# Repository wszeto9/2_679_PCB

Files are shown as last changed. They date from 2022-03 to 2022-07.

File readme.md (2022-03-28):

# 2.679/2.007 Carrier Board
High Power throughput board for the 2.007 "Legacy" Robotics Competiton @ MIT, Spring 2022

[Interactive BOM](https://htmlpreview.github.io/?https://raw.githubusercontent.com/wszeto9/2_679_PCB/main/bom/ibom.html)

<h2> Features:</h2>
<ul>
<li>20A socketable fused input</li>
<li>Reverse polarity protection with warning lights and buzzer to alert incorrect wiring</li>
<li>9V USB-C Power Delivery Input to run off larger battery packs during testing</li>
<li>Protection Circuit to prevent USB-C from backcharging battery</li>
<li>Motor headers with 8.2V Output</li>
<li>Adjustable Servo voltage from 5V to Battery voltage</li>
<li>6A Syncronous Buck converter to reduce the voltage difference between the servo voltage and battery boltage</li>
<li>16 Actuator Ports (8 individually controllable)</li>
<li>Comparator Circuit for light based start signal, directly wired to an Arduino Interrupt</li>
<li>Mechanically Adjustable trigger point for photoresistor interrupt input</li>
<li>8-channel RC controller input for compatability with Gobilda RC Receiver</li>
<li>MPU6050 and LSM6DS33 Header for heading measurements with interrupt pins connected to D2</li>
<li> 5V and 3.3V I2C headers for a multitude of sensor inputs</li>
<li>ARGB Debugging LEDs to offer more variations of debugging signals</li>
<li>ARGB Header to decorate robot in <i><b>light</b></i></li>
<li>Breakout boards for Hall Effect Sensors, In-Line current sensors, and I/O Breakout boards </li>
<li>Fun Silkscreen messages for my favorite professors </li>
</ul>

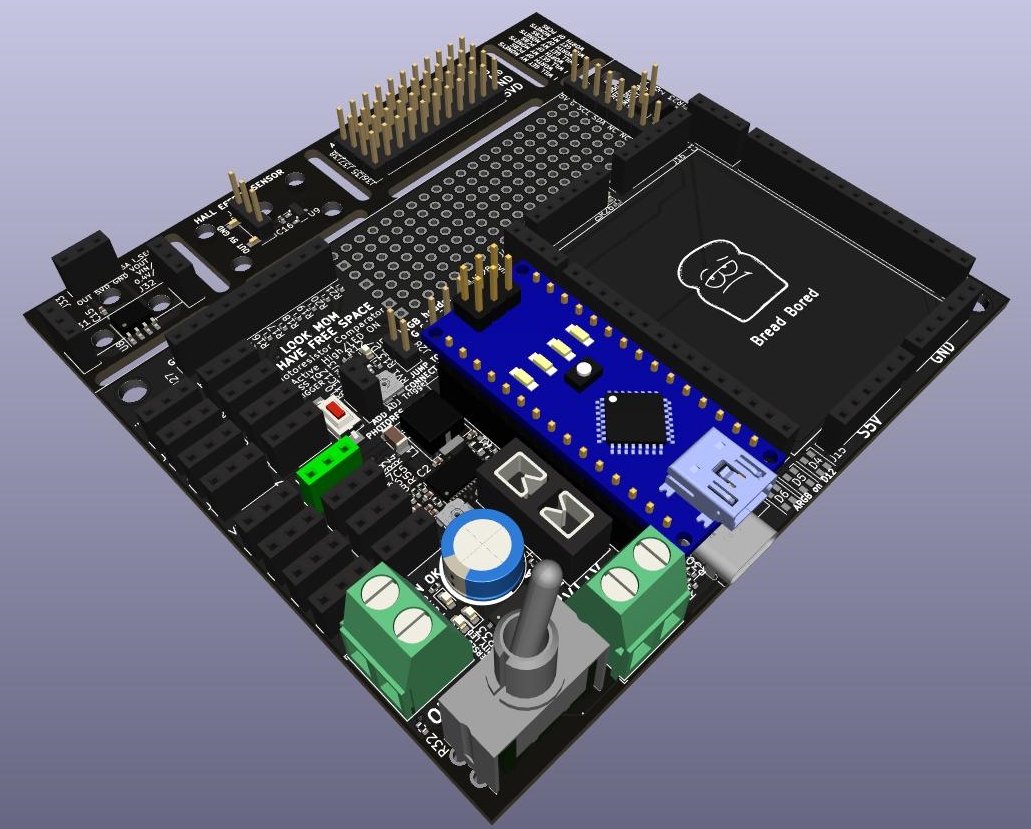
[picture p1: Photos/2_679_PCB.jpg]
3D Assembled

PCBA

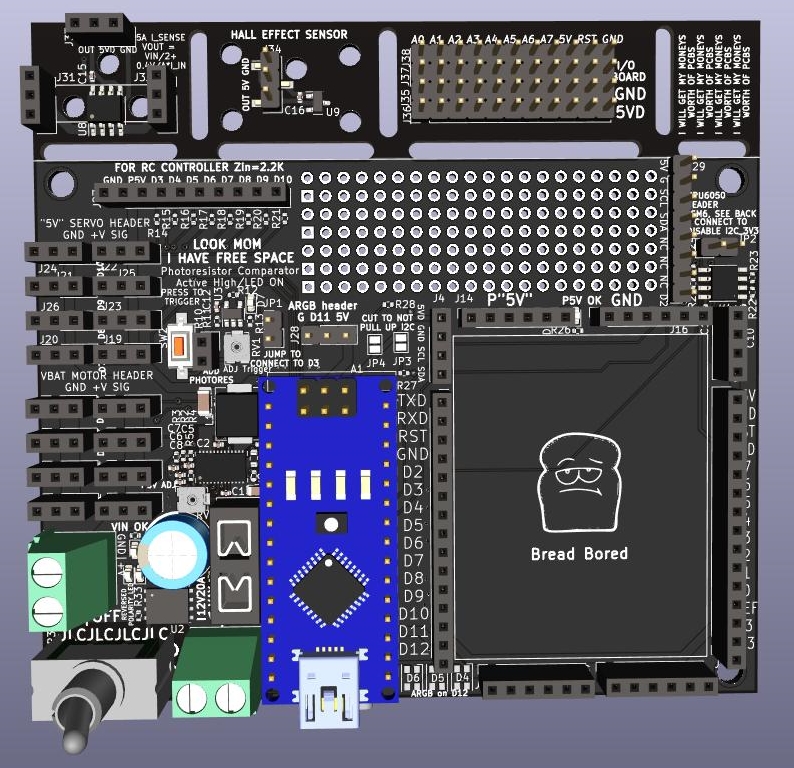
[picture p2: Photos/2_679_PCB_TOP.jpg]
Top

Top

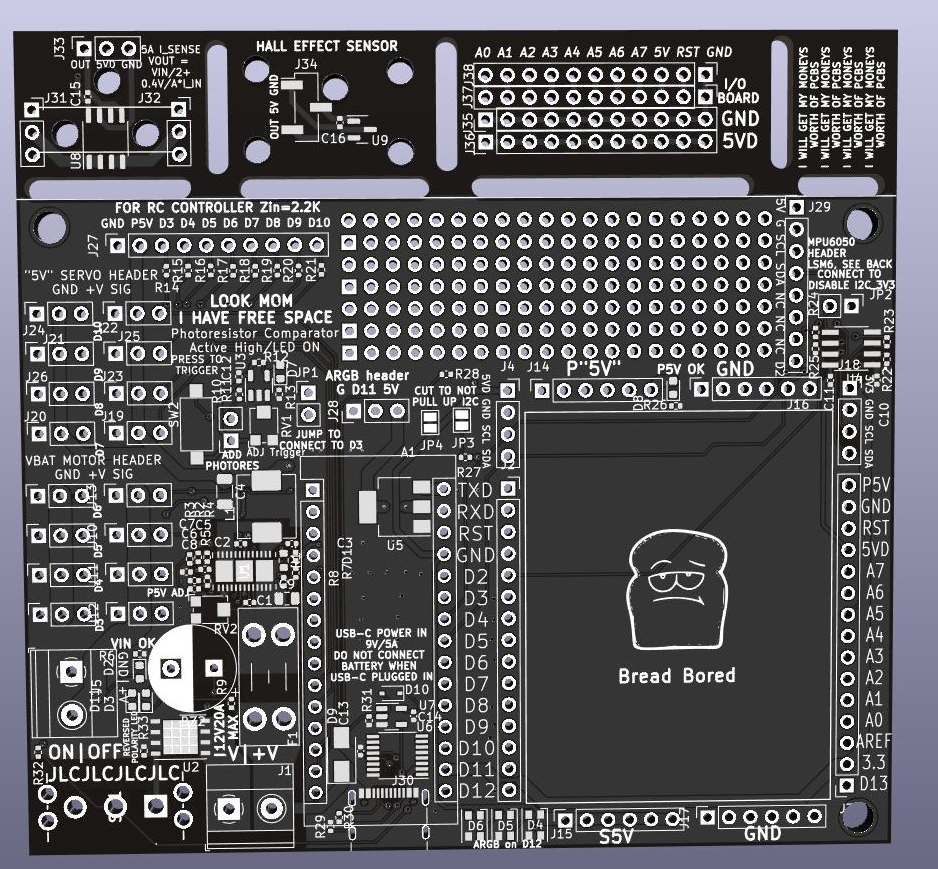
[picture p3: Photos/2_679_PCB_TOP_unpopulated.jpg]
Top_unpopulated

Top Unpopulated Board

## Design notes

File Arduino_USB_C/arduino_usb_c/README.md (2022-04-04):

# 2.007 Power Distribution Board
Battery protection circuit for 2.007 "Legacy" Robotics Competiton @ MIT, Spring 2022

[Interactive BOM](https://htmlpreview.github.io/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)

<h2> Features:</h2>
<ul>
<li>20A socketable fused input</li>
<li>Reverse polarity protection</li>
<li> Voltage Monitoring components to prevent overdischarging of batteries </li>
  <li> Black colored Arduino Nano for looks </li>
  <li> Op-Amp breakout board for additional gain on current sensors</li>
</ul>

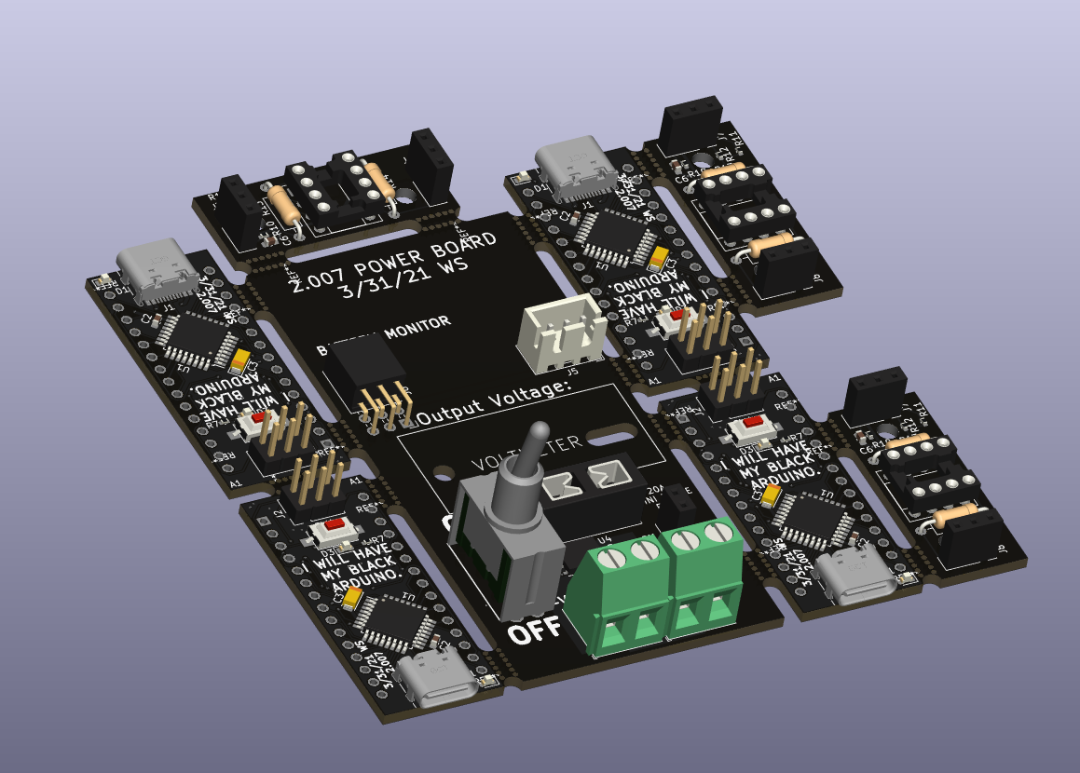
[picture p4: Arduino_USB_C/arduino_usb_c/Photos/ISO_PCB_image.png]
3D Assembled

PCBA

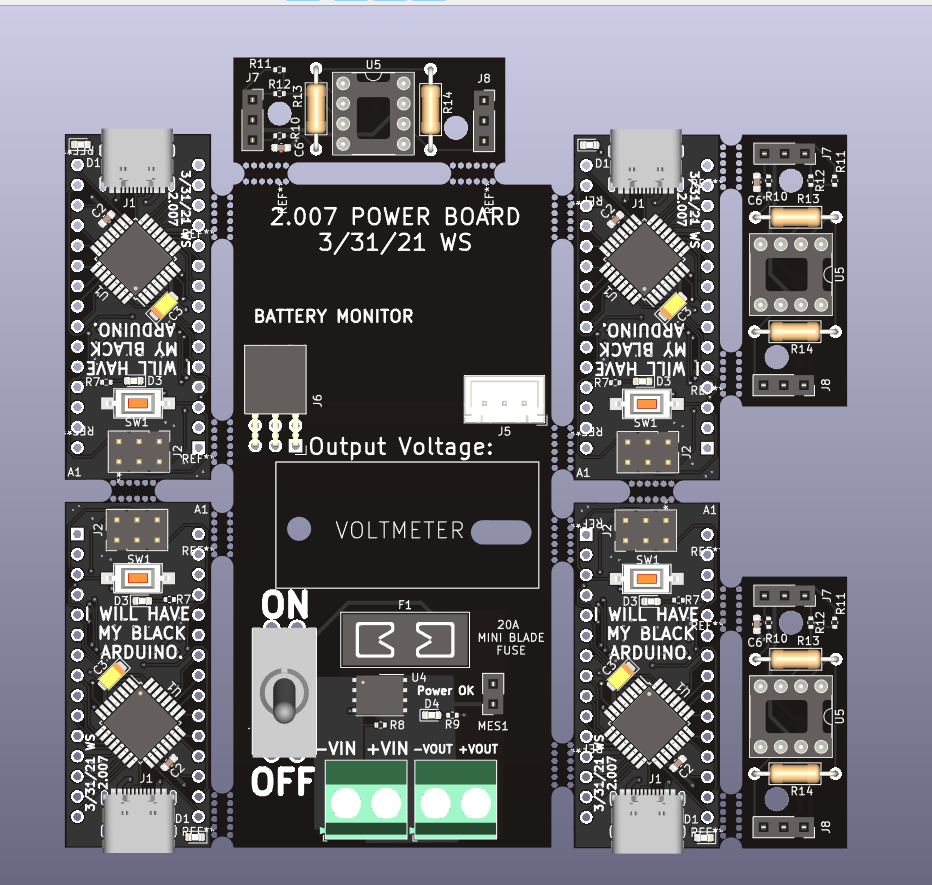
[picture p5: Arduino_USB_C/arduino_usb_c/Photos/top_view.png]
Top

Top

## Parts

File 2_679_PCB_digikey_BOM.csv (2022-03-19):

Item | Qty | Reference(s) | Value | LibPart | Footprint | Datasheet | Digikey
1 | 1 | A1 | Arduino_Nano_v3.x | MCU_Module:Arduino_Nano_v3.x | Module:Arduino_Nano | http://www.mouser.com/pdfdocs/Gravitech_Arduino_Nano3_0.pdf | 1738-1026-ND
2 | 1 | BZ2 | Buzzer | Device:Buzzer | Capacitor_THT:CP_Radial_D10.0mm_P5.00mm | https://www.digikey.com/en/products/detail/pui-audio-inc/AI-1027-TWT-5V-2-R/5011389 | 668-1454-ND
11 | 1 | D1 | D_Schottky | Device:D_Schottky | Diode_SMD:D_0402_1005Metric | https://www.digikey.com/en/products/detail/comchip-technology/CDBQR0130R/1973506 | 641-1272-1-ND
13 | 3 | D4, D5, D6 | 3528 ARGB LED | :SK6812MINI_1 | LED_SMD:LED_Cree-PLCC4_3.2x2.8mm_CCW | https://www.digikey.com/en/products/detail/american-bright-optoelectronics-corporation/BB-HRGB32M-TRB-C/13179345 | 2007-BB-HRGB32M-TRB-CCT-ND
16 | 1 | F1 | 20A | Device:Fuse_Small | Fuse:Fuseholder_Blade_Mini_Keystone_3568 | https://www.digikey.com/en/products/detail/keystone-electronics/3568/2137306 | 36-3568-ND
17 | 2 | J1, J5 | POWER_IN | Connector:Screw_Terminal_01x02 | TerminalBlock_Phoenix:TerminalBlock_Phoenix_MKDS-1,5-2_1x02_P5.00mm_Horizontal | https://www.digikey.com/en/products/detail/te-connectivity-amp-connectors/796949-2/2223908 | 796949-2-ND
18 | 2 | J2,J3 | ARDUINO_HEADER_1 | Connector:Conn_01x15_Female | Connector_PinSocket_2.54mm:PinSocket_1x15_P2.54mm_Vertical | https://www.digikey.com/en/products/detail/sullins-connector-solutions/PPTC151LFBN-RC/810153 | S7013-ND
20 | 2 | J4, J18 | I2C_5V | Connector:Conn_01x04_Female | Connector_PinSocket_2.54mm:PinSocket_1x04_P2.54mm_Vertical | https://www.digikey.com/en/products/detail/sullins-connector-solutions/PPTC041LFBN-RC/810144 | S7002-ND
22 | 20 | J6, J7, J8, J9, J10, J11, J12, J13, J19, J20, J21, J22, J23, J24, J25, J26, J31, J32, J33, J28 | DC Motor Header | Connector:Conn_01x03_Female | Connector_PinSocket_2.54mm:PinSocket_1x03_P2.54mm_Vertical | https://www.digikey.com/en/products/detail/sullins-connector-solutions/PPPC031LFBN-RC/810175 | S7036-ND
23 | 4 | J14, J15, J16, J17 | Conn_01x06_Female | Connector:Conn_01x06_Female | Connector_PinSocket_2.54mm:PinSocket_1x06_P2.54mm_Vertical | ~https://www.digikey.com/en/products/detail/sullins-connector-solutions/PPTC061LFBN-RC/810145 | S7004-ND
26 | 1 | J27 | RC IN | Connector:Conn_01x10_Female | Connector_PinSocket_2.54mm:PinSocket_1x10_P2.54mm_Vertical | https://www.digikey.com/en/products/detail/sullins-connector-solutions/PPPC101LFBN-RC/810182 | S7043-ND
28 | 1 | J29 | MPU6050 | Connector:Conn_01x08_Female | Connector_PinHeader_2.54mm:PinHeader_1x08_P2.54mm_Vertical | ~ | S7006-ND
29 | 1 | J30 | USB_C_Receptacle_USB2.0 | Connector:USB_C_Receptacle_USB2.0 | Connector_USB:USB_C_Receptacle_Palconn_UTC16-G | https://www.usb.org/sites/default/files/documents/usb_type-c.zip | 2073-USB4105-GF-ACT-ND
33 | 1 | J34 | HALL_OUT | Connector:Conn_01x03_Female | Connector_PinHeader_2.54mm:PinHeader_1x03_P2.54mm_Vertical_SMD_Pin1Left | ~ | S5595-ND
34 | 4 | J35, J36, J37, J38 | Conn_01x11_Male | Connector:Conn_01x11_Male | Connector_PinHeader_2.54mm:PinHeader_1x11_P2.54mm_Vertical | ~ | S7009-ND
35 | 2 | JP1, JP2 | Jumper_2_Bridged | Jumper:Jumper_2_Bridged | Connector_PinHeader_2.54mm:PinHeader_1x02_P2.54mm_Vertical | ~ | S9000-ND
37 | 1 | L1 | 2.2uH 8A | pspice:INDUCTOR | Inductor_SMD:L_Abracon_ASPI-0630LR | https://www.digikey.com/en/products/detail/sumida-america-components-inc/0630CDMCCDS-2R2MC/5812456 | 308-2464-1-ND
47 | 1 | R10 | R_Photo | Device:R_Photo | Connector_PinSocket_2.54mm:PinSocket_1x02_P2.54mm_Vertical | https://www.digikey.com/en/products/detail/sullins-connector-solutions/PPTC021LFBN-RC/810142 | S7000-ND
51 | 2 | RV1, RV2 | 200k | Device:R_Potentiometer_Small | Potentiometer_SMD:Potentiometer_Bourns_TC33X_Vertical | ~ | TC33X-2-204ECT-ND
52 | 1 | SW1 | SW_SPST | Switch:SW_SPST | Switch:M2012SS2W13 | https://www.digikey.com/en/products/detail/nkk-switches/M2012SS2W13/1052259 | 360-2840-ND
53 | 1 | SW2 | SW_Push_Open | Switch:SW_Push_Open | Button_Switch_SMD:SW_SPST_CK_RS282G05A3 | https://www.digikey.com/en/products/detail/c-k/PTS636-SK25J-SMTR-LFS/10071739 | CKN12326-1-ND
57 | 1 | U1 | SP7652ER-L/TR | 2022-03-08_23-16-42:SP7652ER-L{slash}TR | sp7652:SP7652ER-L&slash_TR | https://www.digikey.com/en/products/detail/maxlinear-inc/SP7652ER-L-TR/2472248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 | 1016-1843-1-ND
58 | 1 | U2 | AON6558 | AON6558:AON6558 | Package_DFN_QFN:DFN-8-1EP_6x5mm_P1.27mm_EP4x4mm | https://www.digikey.com/en/products/detail/alpha-omega-semiconductor-inc/AON6558/4764695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 | 785-1670-1-ND
59 | 1 | U3 | LMV331 | Comparator:LMV331 | Package_TO_SOT_SMD:SOT-23-5 | https://www.digikey.com/en/products/detail/texas-instruments/LMV331M5X-NOPB/334971 | LMV331M5X/NOPBCT-ND
63 | 1 | U7 | BU4SU69G2 | 74xGxx:74LVC1GU04DRL | Package_TO_SOT_SMD:SOT-23-5 | https://www.digikey.com/en/products/detail/rohm-semiconductor/BU4SU69G2-TR/658725 | BU4SU69G2CT-ND

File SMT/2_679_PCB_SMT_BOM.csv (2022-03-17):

Comment | Designator | Footprint | LCSC
Arduino_Nano_v3.x | A1 | Module:Arduino_Nano
Buzzer | BZ2 | Capacitor_THT:CP_Radial_D10.0mm_P5.00mm
22nF | C1 | Capacitor_SMD:C_0402_1005Metric | C1532
0.1uF | C10,C11,C12,C15,C16 | Capacitor_SMD:C_0402_1005Metric | C307331
1uF | C2,C3,C13,C14 | Capacitor_SMD:C_0402_1005Metric | C52923
47uF | C4 | Capacitor_SMD:C_1206_3216Metric | C96123
100pF | C5,C7 | Capacitor_SMD:C_0402_1005Metric | C1546
22pF | C6 | Capacitor_SMD:C_0402_1005Metric | C1555
1nF | C8 | Capacitor_SMD:C_0402_1005Metric | C1523
22uF | C9 | Capacitor_SMD:C_0805_2012Metric | C45783
D_Schottky | D1 | Diode_SMD:D_0402_1005Metric
1N5819WS | D10 | Diode_SMD:D_SOD-323 | C191023
LED | D2,D3,D7,D8,D11 | LED_SMD:LED_0603_1608Metric | C2290
3528 ARGB LED | D4,D5,D6 | LED_SMD:LED_Cree-PLCC4_3.2x2.8mm_CCW
SS54 | D9 | Diode_SMD:D_SMA | C22452
20A | F1 | Fuse:Fuseholder_Blade_Mini_Keystone_3568
POWER_IN | J1 | TerminalBlock_Phoenix:TerminalBlock_Phoenix_MKDS-1,5-2_1x02_P5.00mm_Horizontal
Conn_01x06_Female | J14,J15,J16,J17 | Connector_PinSocket_2.54mm:PinSocket_1x06_P2.54mm_Vertical
I2C_3V3 | J18 | Connector_PinSocket_2.54mm:PinSocket_1x04_P2.54mm_Vertical
Servo Header | J19,J20,J21,J22,J23,J24,J25,J26 | Connector_PinSocket_2.54mm:PinSocket_1x03_P2.54mm_Vertical
ARDUINO_HEADER_1 | J2 | Connector_PinSocket_2.54mm:PinSocket_1x15_P2.54mm_Vertical
RC IN | J27 | Connector_PinSocket_2.54mm:PinSocket_1x10_P2.54mm_Vertical
NEOPIXEL | J28 | Connector_PinHeader_2.54mm:PinHeader_1x03_P2.54mm_Vertical
MPU6050 | J29 | Connector_PinHeader_2.54mm:PinHeader_1x08_P2.54mm_Vertical
ARDUINO_HEADER_2 | J3 | Connector_PinSocket_2.54mm:PinSocket_1x15_P2.54mm_Vertical
USB_C_Receptacle_USB2.0 | J30 | Connector_USB:USB_C_Receptacle_Palconn_UTC16-G
I_IN | J31 | Connector_PinSocket_2.54mm:PinSocket_1x03_P2.54mm_Vertical
I_OUT | J32 | Connector_PinSocket_2.54mm:PinSocket_1x03_P2.54mm_Vertical
D_OUT | J33 | Connector_PinSocket_2.54mm:PinSocket_1x03_P2.54mm_Vertical
HALL_OUT | J34 | Connector_PinHeader_2.54mm:PinHeader_1x03_P2.54mm_Vertical_SMD_Pin1Left
Conn_01x11_Male | J35,J36,J37,J38 | Connector_PinHeader_2.54mm:PinHeader_1x11_P2.54mm_Vertical
I2C_5V | J4 | Connector_PinSocket_2.54mm:PinSocket_1x04_P2.54mm_Vertical
POWER_OUT | J5 | TerminalBlock_Phoenix:TerminalBlock_Phoenix_MKDS-1,5-2-5.08_1x02_P5.08mm_Horizontal
DC Motor Header | J6,J7,J8,J9,J10,J11,J12,J13 | Connector_PinSocket_2.54mm:PinSocket_1x03_P2.54mm_Vertical
Jumper_2_Bridged | JP1,JP2 | Connector_PinHeader_2.54mm:PinHeader_1x02_P2.54mm_Vertical
Jumper_2_Bridged | JP3,JP4 | Jumper:SolderJumper-2_P1.3mm_Bridged_Pad1.0x1.5mm
2.2uH 8A | L1 | Inductor_SMD:L_Abracon_ASPI-0630LR
5.1R | R1 | Resistor_SMD:R_0603_1608Metric | C25197
R_Photo | R10 | Connector_PinSocket_2.54mm:PinSocket_1x02_P2.54mm_Vertical
10K | R11,R22,R23,R24,R25,R31 | Resistor_SMD:R_0402_1005Metric | C25744
2.2K | R14,R15,R16,R17,R18,R19,R20,R21 | Resistor_SMD:R_0402_1005Metric | C25879
68K | R2,R33 | Resistor_SMD:R_0402_1005Metric | C36871
4.7k | R27,R28 | Resistor_SMD:R_0402_1005Metric | C25900
220k | R3 | Resistor_SMD:R_0402_1005Metric | C25767
5.1k | R4,R29,R30 | Resistor_SMD:R_0402_1005Metric | C25905
12k | R5 | Resistor_SMD:R_0402_1005Metric | C25752
1K | R6,R12,R13,R26,R32 | Resistor_SMD:R_0402_1005Metric | C11702
15k | R7 | Resistor_SMD:R_0402_1005Metric | C25756
10k | R8 | Resistor_SMD:R_0402_1005Metric | C25744
470R | R9 | Resistor_SMD:R_0402_1005Metric | C25117
200k | RV1,RV2 | Potentiometer_SMD:Potentiometer_Bourns_TC33X_Vertical | C25764
SW_SPST | SW1 | Switch:M2012SS2W13
SW_Push_Open | SW2 | Button_Switch_SMD:SW_SPST_CK_RS282G05A3
SW_P3 | SW3 | Jumper:SolderJumper-3_P1.3mm_Bridged12_Pad1.0x1.5mm
SW_P4 | SW4 | Jumper:SolderJumper-3_P1.3mm_Bridged12_Pad1.0x1.5mm
SW_SPST | SW5 | Jumper:SolderJumper-2_P1.3mm_Open_TrianglePad1.0x1.5mm
SP7652ER-L/TR | U1 | sp7652:SP7652ER-L&slash_TR
AON6558 | U2 | Package_DFN_QFN:DFN-8-1EP_6x5mm_P1.27mm_EP4x4mm
LMV331 | U3 | Package_TO_SOT_SMD:SOT-23-5
TCA9517DR | U4 | TCA9517:SOIC127P599X175-8N
AMS1117-5.0 | U5 | Package_TO_SOT_SMD:SOT-223-3_TabPin2
IP2721 | U6 | Package_SO:TSSOP-16_4.4x5mm_P0.65mm
BU4SU69G2 | U7 | Package_TO_SOT_SMD:SOT-23-5
CC6920BSO-5A | U8 | Package_SO:SOP-8_3.9x4.9mm_P1.27mm | C2880430
DRV5033AJxDBZ | U9 | Package_TO_SOT_SMD:SOT-23

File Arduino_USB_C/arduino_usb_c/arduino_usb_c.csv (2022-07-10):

Item | Qty | Reference(s) | Value | LibPart | Footprint | Datasheet | Digikey
2 | 4 | C1, C2, C5, C9 | 100nF | Device:C_Small | Capacitor_SMD:C_0603_1608Metric | ~ | 490-4779-1-ND
3 | 2 | C3, C8 | 4.7uF 16V Tant | Device:C_Polarized_Small_US | Capacitor_Tantalum_SMD:CP_EIA-3216-10_Kemet-I | ~ | 478-3868-1-ND
4 | 4 | C4, C6, C7, C10 | 1uF | Device:C_Small | Capacitor_SMD:C_0603_1608Metric | ~ | 490-1543-1-ND
5 | 3 | D1, D3, D4 | LED | Device:LED | LED_SMD:LED_0603_1608Metric | ~ | 475-2512-1-ND
6 | 1 | D2 | D_Schottky | Device:D_Schottky | Diode_SMD:D_SMA | ~ | 641-1015-1-ND
7 | 1 | F1 | Fuse | Device:Fuse | Fuse:Fuseholder_Blade_Mini_Keystone_3568 | ~ | 36-3568-ND
8 | 1 | J1 | USB_C_Receptacle_USB2.0 | Connector:USB_C_Receptacle_USB2.0 | Connector_USB:USB_C_Receptacle_Palconn_UTC16-G | https://www.usb.org/sites/default/files/documents/usb_type-c.zip | 2073-USB4105-GF-ACT-ND
9 | 1 | J2 | Conn_02x03_Odd_Even | Connector_Generic:Conn_02x03_Odd_Even | Connector_PinHeader_2.54mm:PinHeader_2x03_P2.54mm_Vertical | https://www.digikey.com/en/products/detail/harwin-inc/M20-9980346/3728085 | 952-2121-ND
10 | 2 | J3, J4 | Screw_Terminal_01x02 | Connector:Screw_Terminal_01x02 | TerminalBlock_Phoenix:TerminalBlock_Phoenix_MKDS-1,5-2-5.08_1x02_P5.08mm_Horizontal | ~ | 796949-2-ND
11 | 1 | J5 | Conn_01x03_Male | Connector:Conn_01x03_Male | Connector_JST:JST_XH_B3B-XH-A_1x03_P2.50mm_Vertical | ~ | 455-1990-ND
12 | 1 | J6 | Conn_02x03_Odd_Even | Connector_Generic:Conn_02x03_Odd_Even | Connector_PinSocket_2.54mm:PinSocket_2x03_P2.54mm_Horizontal | ~ | S5517-ND
14 | 1 | MES1 | Voltmeter_DC | Device:Voltmeter_DC | Connector_PinSocket_2.54mm:PinSocket_1x02_P2.54mm_Vertical | ~ | 1568-1700-ND
15 | 6 | R1, R2, R3, R4, R7, R9 | 1K | Device:R_Small_US | Resistor_SMD:R_0402_1005Metric | ~ | RNCP0805FTD1K00CT-ND
16 | 2 | R5, R6 | 5.1K 1% | Device:R_Small_US | Resistor_SMD:R_0402_1005Metric | ~ | RMCF0805FT5K10CT-ND
17 | 4 | R8, R10, R11, R12 | 10k | Device:R_Small_US | Resistor_SMD:R_0402_1005Metric | ~ | RMCF0402FT10K0CT-ND
20 | 1 | SW1 | SW_SPST | Switch:SW_SPST | Button_Switch_SMD:SW_SPST_CK_RS282G05A3 | ~ | CKN12326-1-ND
25 | 1 | U4 | AON6558 | AON6558:AON6558 | Package_DFN_QFN:DFN-8-1EP_6x5mm_P1.27mm_EP4x4mm |  | 785-1670-1-ND
27 | 1 | Y1 | Crystal_GND2_Small | Device:Crystal_GND2_Small | Crystal:Resonator_SMD_Murata_CSTxExxV-3Pin_3.0x1.1mm | ~ | 490-17950-1-ND

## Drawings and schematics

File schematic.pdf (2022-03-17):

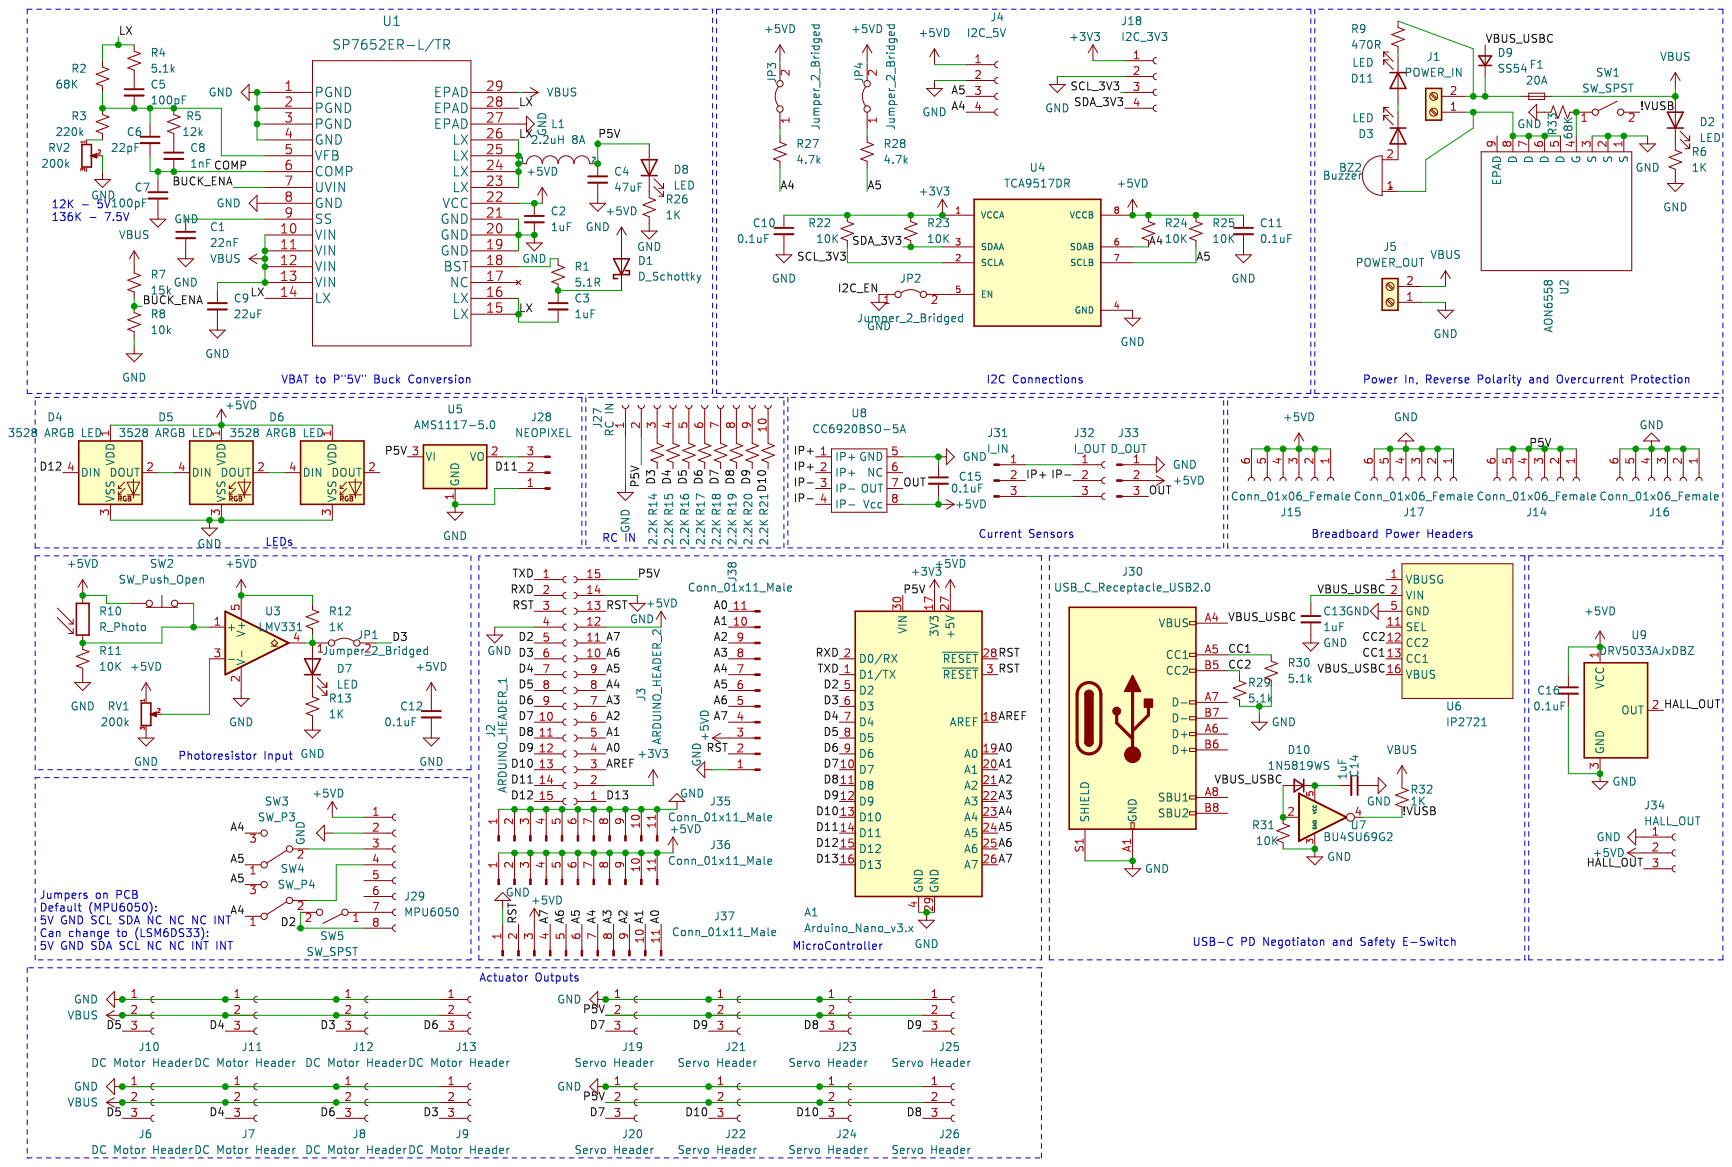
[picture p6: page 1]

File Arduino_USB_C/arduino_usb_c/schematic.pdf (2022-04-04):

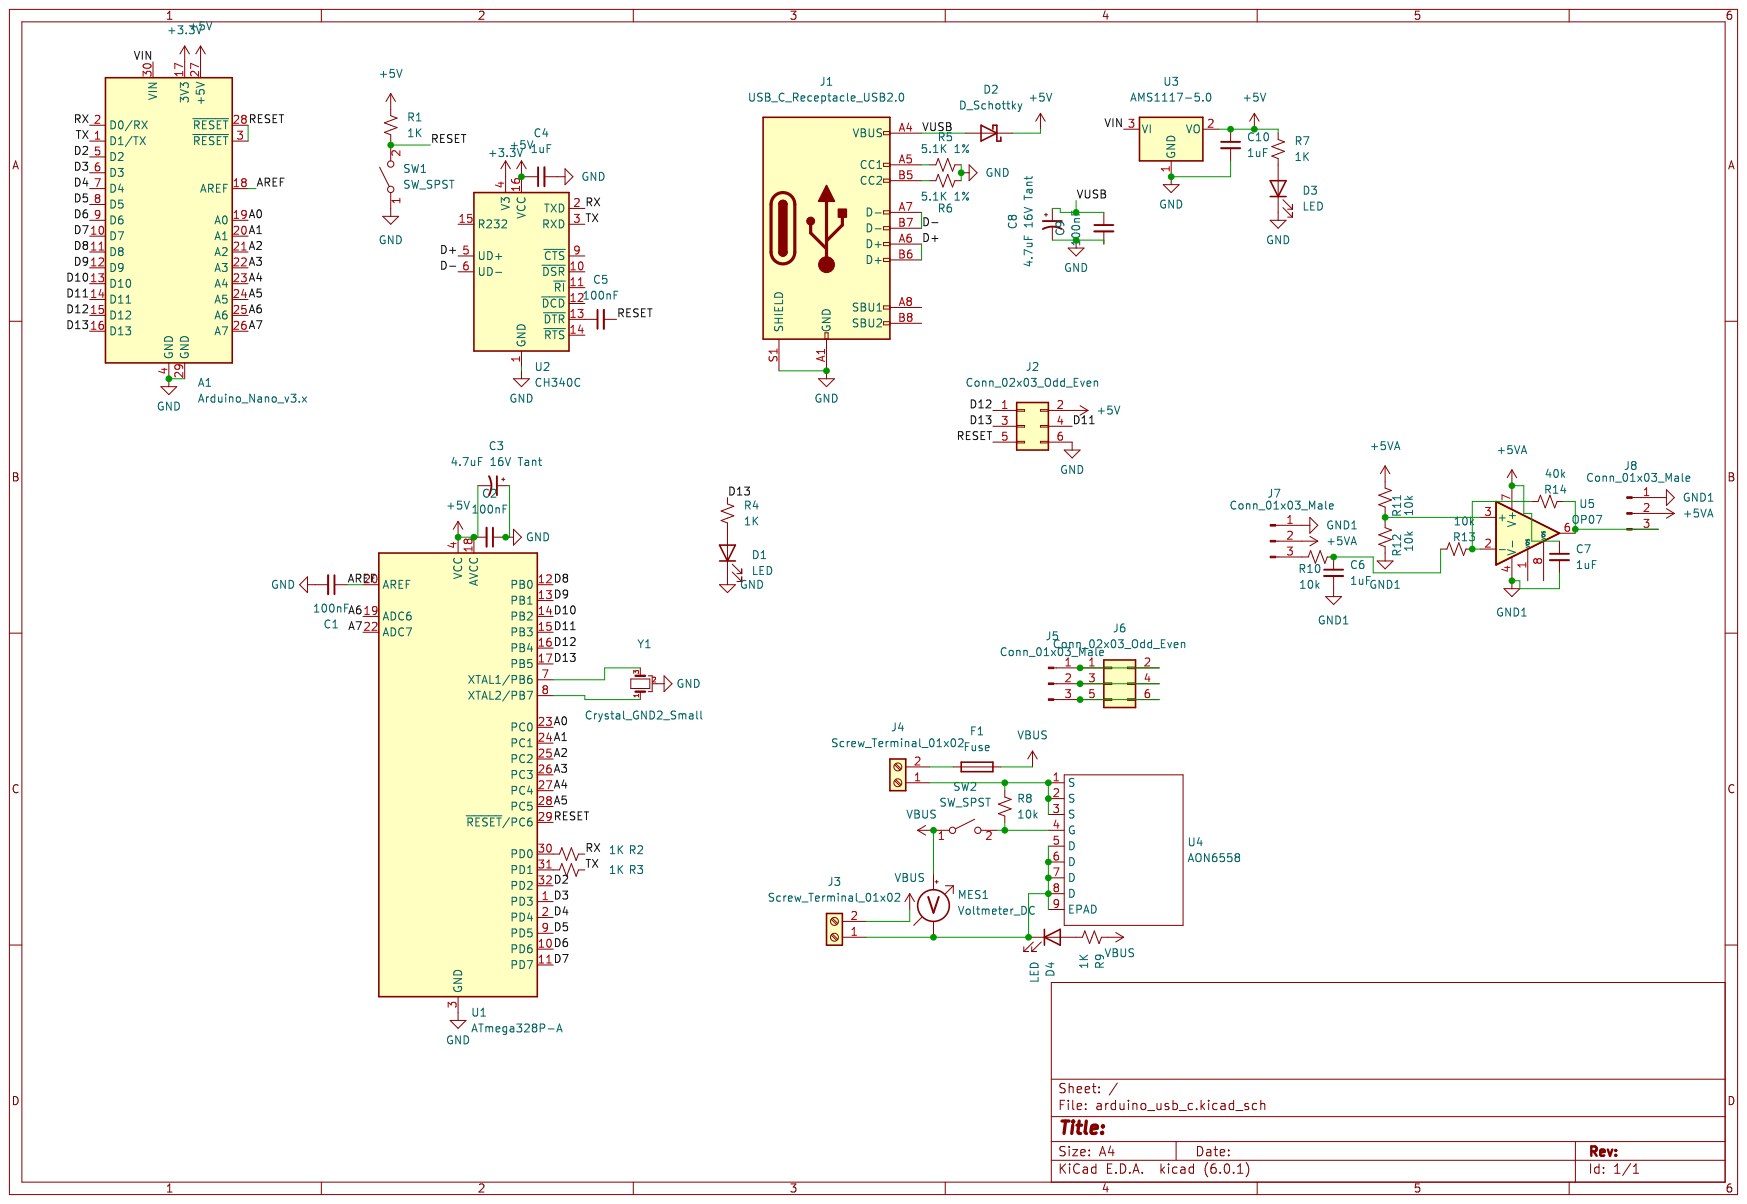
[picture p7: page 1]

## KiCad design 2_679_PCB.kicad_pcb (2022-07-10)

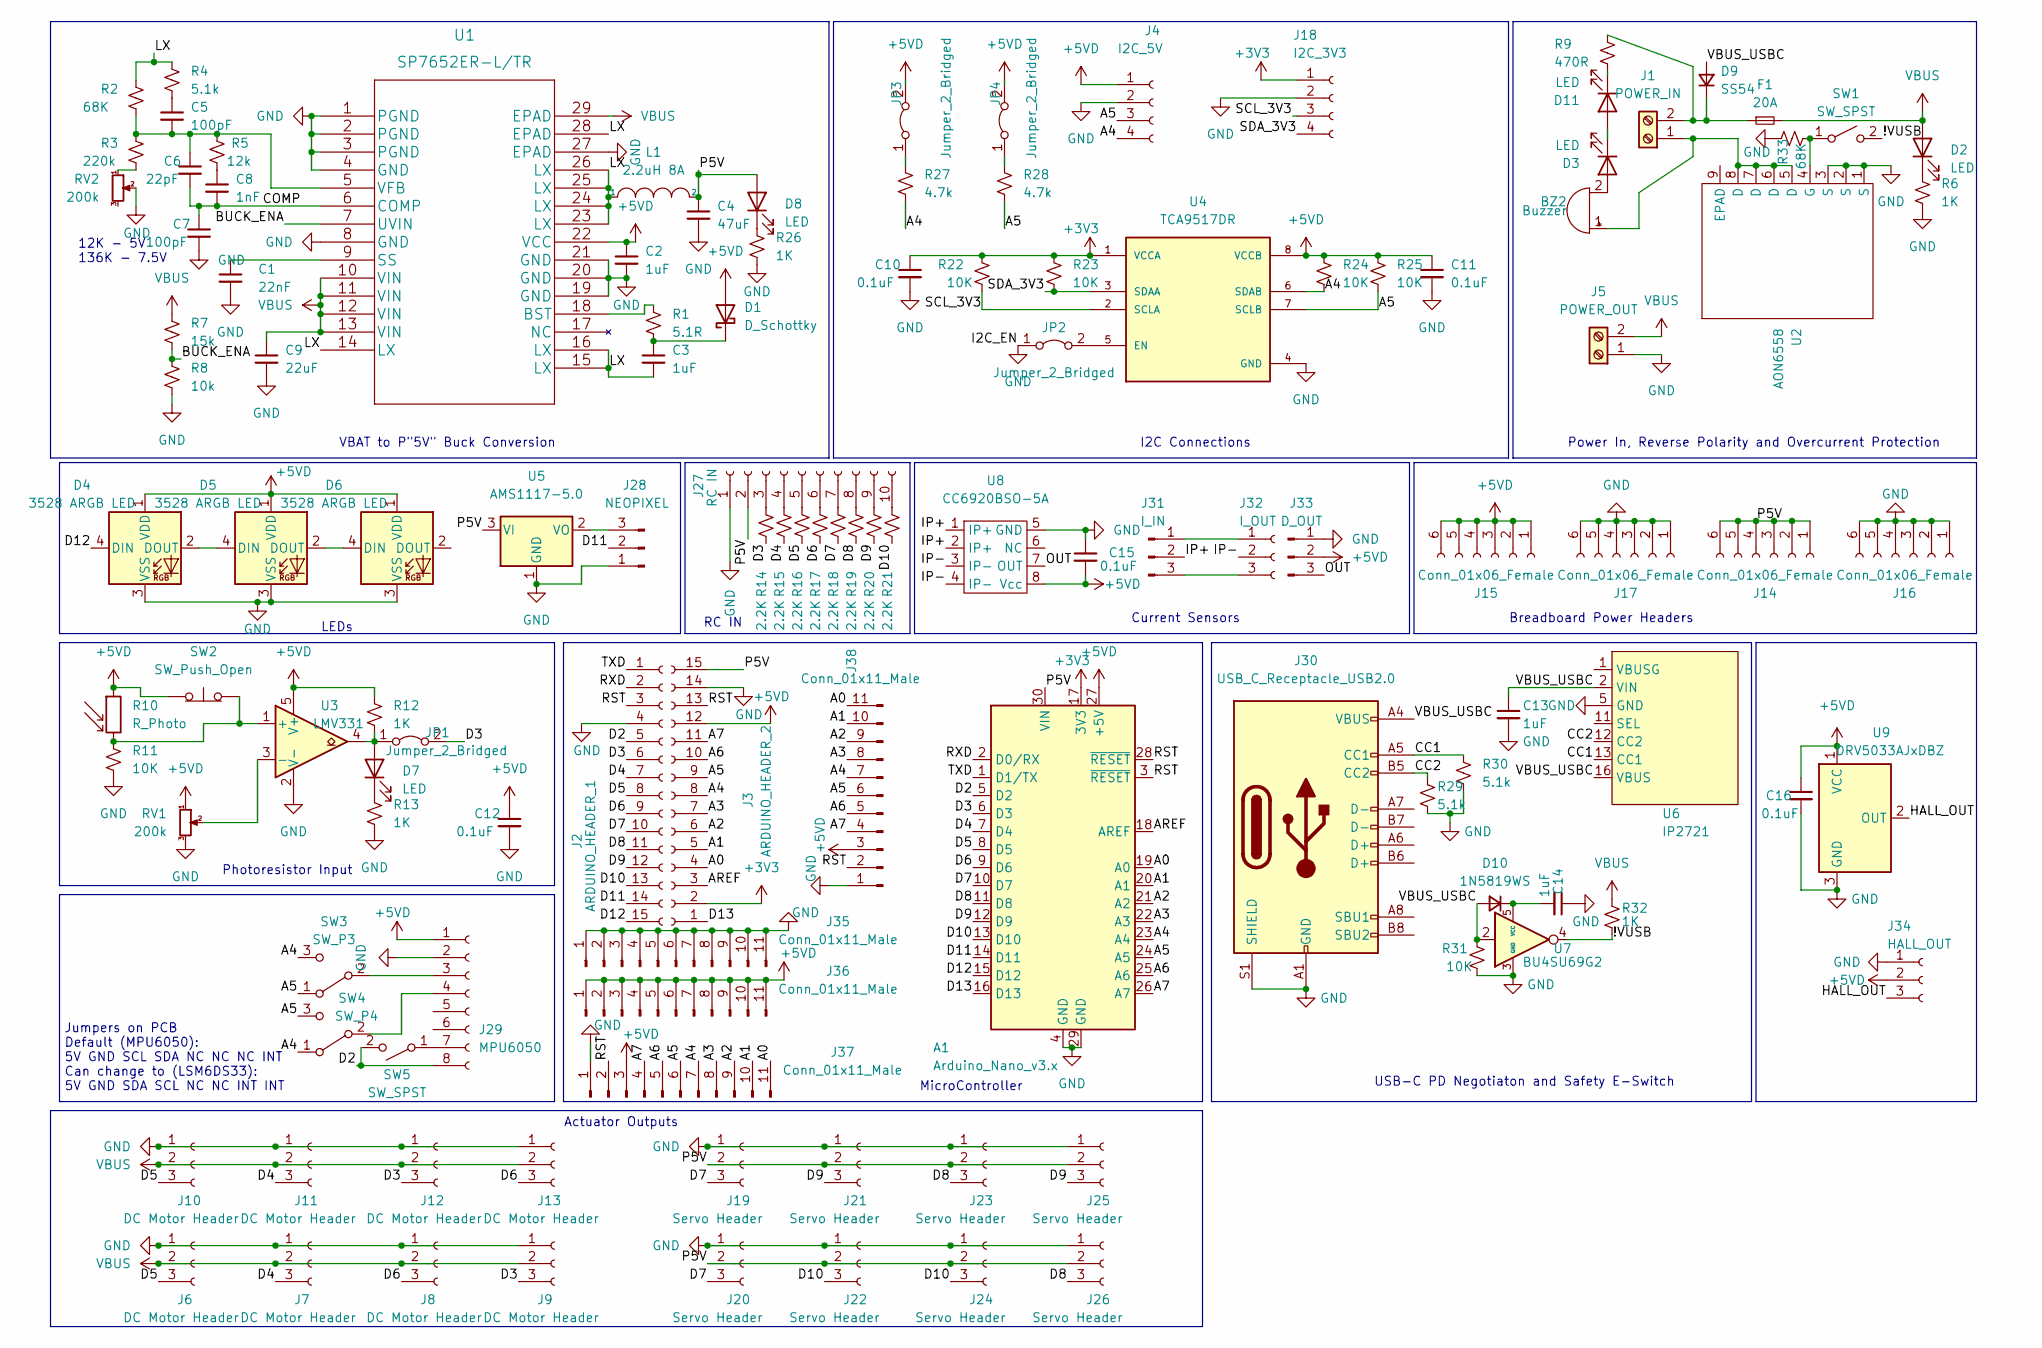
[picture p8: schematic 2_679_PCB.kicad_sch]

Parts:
A1: Arduino_Nano_v3.x; Arduino_Nano; Digikey 1738-1026-ND
BZ2: Buzzer; CP_Radial_D10.0mm_P5.00mm; Digikey 668-1454-ND
C1: 22nF; C_0402_1005Metric; LCSC C1532
C2, C3, C13, C14: 1uF; C_0402_1005Metric; LCSC C52923
C4: 47uF; C_1206_3216Metric; LCSC C96123
C5, C7: 100pF; C_0402_1005Metric; LCSC C1546
C6: 22pF; C_0402_1005Metric; LCSC C1555
C8: 1nF; C_0402_1005Metric; LCSC C1523
C9: 22uF; C_0805_2012Metric; LCSC C45783
C10, C11, C12, C15, C16: 0.1uF; C_0402_1005Metric; LCSC C307331
D1: D_Schottky; D_0402_1005Metric; Digikey 641-1272-1-ND
D2: LED; LED_0603_1608Metric; LCSC C2290
D3, D11: LED; LED_0603_1608Metric; LCSC C2286
D4, D5, D6: 3528 ARGB LED; LED_Cree-PLCC4_3.2x2.8mm_CCW; Digikey 2007-BB-HRGB32M-TRB-CCT-ND
D7: LED; LED_0603_1608Metric; LCSC C72043
D8: LED; LED_0603_1608Metric; LCSC C72038
D9: SS54; D_SMA; LCSC C22452
D10: 1N5819WS; D_SOD-323; LCSC C191023
F1: 20A; Fuseholder_Blade_Mini_Keystone_3568; Digikey 36-3568-ND
J1: POWER_IN; TerminalBlock_Phoenix_MKDS-1,5-2_1x02_P5.00mm_Horizontal; Digikey 796949-2-ND
J2: ARDUINO_HEADER_1; PinSocket_1x15_P2.54mm_Vertical; Digikey S7013-ND
J3: ARDUINO_HEADER_2; PinSocket_1x15_P2.54mm_Vertical; Digikey S7013-ND
J4: I2C_5V; PinSocket_1x04_P2.54mm_Vertical; Digikey S7002-ND
J5: POWER_OUT; TerminalBlock_Phoenix_MKDS-1,5-2-5.08_1x02_P5.08mm_Horizont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; Digikey 796949-2-ND
J6, J7, J8, J9, J10, J11, J12, J13: DC Motor Header; PinSocket_1x03_P2.54mm_Vertical; Digikey S7036-ND
J14, J15, J16, J17: Conn_01x06_Female; PinSocket_1x06_P2.54mm_Vertical; Digikey S7004-ND
J18: I2C_3V3; PinSocket_1x04_P2.54mm_Vertical; Digikey S7002-ND
J19, J20, J21, J22, J23, J24, J25, J26: Servo Header; PinSocket_1x03_P2.54mm_Vertical; Digikey S7036-ND
J27: RC IN; PinSocket_1x10_P2.54mm_Vertical; Digikey S7043-ND
J28: NEOPIXEL; PinHeader_1x03_P2.54mm_Vertical; Digikey S7036-ND
J29: MPU6050; PinHeader_1x08_P2.54mm_Vertical; Digikey S7006-ND
J30: USB_C_Receptacle_USB2.0; USB_C_Receptacle_Palconn_UTC16-G; Digikey 2073-USB4105-GF-ACT-ND
J31: I_IN; PinSocket_1x03_P2.54mm_Vertical; Digikey S7036-ND
J32: I_OUT; PinSocket_1x03_P2.54mm_Vertical; Digikey S7036-ND
J33: D_OUT; PinSocket_1x03_P2.54mm_Vertical; Digikey S7036-ND
J34: HALL_OUT; PinHeader_1x03_P2.54mm_Vertical_SMD_Pin1Left; Digikey S5595-ND
J35, J36, J37, J38: Conn_01x11_Male; PinHeader_1x11_P2.54mm_Vertical; Digikey S7009-ND
JP1, JP2: Jumper_2_Bridged; PinHeader_1x02_P2.54mm_Vertical
JP3, JP4: Jumper_2_Bridged; SolderJumper-2_P1.3mm_Bridged_Pad1.0x1.5mm
L1: 2.2uH 8A; L_Abracon_ASPI-0630LR; Digikey 308-2464-1-ND
R1: 5.1R; R_0603_1608Metric; LCSC C25197
R2, R33: 68K; R_0402_1005Metric; LCSC C36871
R3: 220k; R_0402_1005Metric; LCSC C25767
R4, R29, R30: 5.1k; R_0402_1005Metric; LCSC C25905
R5: 12k; R_0402_1005Metric; LCSC C25752
R6, R12, R13, R26, R32: 1K; R_0402_1005Metric; LCSC C11702
R7: 15k; R_0402_1005Metric; LCSC C25756
R8: 10k; R_0402_1005Metric; LCSC C25744
R9: 470R; R_0402_1005Metric; LCSC C25117
R10: R_Photo; PinSocket_1x02_P2.54mm_Vertical; Digikey S7000-ND
R11, R22, R23, R24, R25, R31: 10K; R_0402_1005Metric; LCSC C25744
R14, R15, R16, R17, R18, R19, R20, R21: 2.2K; R_0402_1005Metric; LCSC C25879
R27, R28: 4.7k; R_0402_1005Metric; LCSC C25900
RV1, RV2: 200k; Potentiometer_Bourns_TC33X_Vertical; Digikey TC33X-2-204ECT-ND
SW1: SW_SPST; M2012SS2W13; Digikey 360-2840-ND
SW2: SW_Push_Open; SW_SPST_CK_RS282G05A3; Digikey CKN12326-1-ND
SW3: SW_P3; SolderJumper-3_P1.3mm_Bridged12_Pad1.0x1.5mm
SW4: SW_P4; SolderJumper-3_P1.3mm_Bridged12_Pad1.0x1.5mm
SW5: SW_SPST; SolderJumper-2_P1.3mm_Open_TrianglePad1.0x1.5mm; Digikey 360-2840-ND
U1: SP7652ER-L/TR; SP7652ER-L&slash_TR; Digikey 1016-1843-1-ND
U2: AON6558; DFN-8-1EP_6x5mm_P1.27mm_EP4x4mm; Digikey 785-1670-1-ND
U3: LMV331; SOT-23-5; Digikey LMV331M5X/NOPBCT-ND
U4: TCA9517DR; SOIC127P599X175-8N; PARTREV D
U5: AMS1117-5.0; SOT-223-3_TabPin2
U6: IP2721; TSSOP-16_4.4x5mm_P0.65mm
U7: BU4SU69G2; SOT-23-5; Digikey BU4SU69G2CT-ND
U8: CC6920BSO-5A; SOP-8_3.9x4.9mm_P1.27mm; LCSC C2880430
U9: DRV5033AJxDBZ; SOT-23

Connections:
+3V3: A1.17 (3V3), C10.1, J3.2, J18.1, R22.1, R23.1, U4.1 (VCCA)
+5VD: A1.27 (+5V), C2.1, C11.1, C12.1, C15.2, C16.1, D1.2 (A), D4.1 (VDD), D5.1 (VDD), D6.1 (VDD), J3.12, J4.1, J15.1, J15.2, J15.3, J15.4, J15.5, J15.6, J29.1, J33.2, J34.2, J36.1, J36.2, J36.3, J36.4, J36.5, J36.6, J36.7, J36.8, J36.9, J36.10, J36.11, J37.3, J38.3, JP3.2 (B), JP4.2 (B), R10.1, R12.1, R24.1, R25.1, RV1.1, SW2.1 (A), U1.22 (VCC), U3.5 (V+), U4.8 (VCCB), U8.8 (Vcc), U9.1 (VCC)
/!VUSB: R32.2, SW1.2 (B), U7.4
/A0: A1.19 (A0), J3.4, J37.11, J38.11
/A1: A1.20 (A1), J3.5, J37.10, J38.10
/A2: A1.21 (A2), J3.6, J37.9, J38.9
/A3: A1.22 (A3), J3.7, J37.8, J38.8
/A4: A1.23 (A4), J3.8, J4.4, J37.7, J38.7, R24.2, R27.2, SW3.3 (C), SW4.1 (A), U4.6 (SDAB)
/A5: A1.24 (A5), J3.9, J4.3, J37.6, J38.6, R25.2, R28.2, SW3.1 (A), SW4.3 (C), U4.7 (SCLB)
/A6: A1.25 (A6), J3.10, J37.5, J38.5
/A7: A1.26 (A7), J3.11, J37.4, J38.4
/AREF: A1.18 (AREF), J3.3
/BUCK_ENA: R7.2, R8.1, U1.7 (UVIN)
/CC1: J30.A5 (CC1), R30.1, U6.13 (CC1)
/CC2: J30.B5 (CC2), R29.1, U6.12 (CC2)
/COMP: C6.2, C7.1, C8.2, U1.6 (COMP)
/D2: A1.5 (D2), J2.5, J29.8, SW5.2 (B)
/D3: A1.6 (D3), J2.6, J9.3, J12.3, JP1.2 (B), R14.1
/D4: A1.7 (D4), J2.7, J7.3, J11.3, R15.1
/D5: A1.8 (D5), J2.8, J6.3, J10.3, R16.1
/D6: A1.9 (D6), J2.9, J8.3, J13.3, R17.1
/D7: A1.10 (D7), J2.10, J19.3, J20.3, R18.1
/D8: A1.11 (D8), J2.11, J23.3, J26.3, R19.1
/D9: A1.12 (D9), J2.12, J21.3, J25.3, R20.1
/D10: A1.13 (D10), J2.13, J22.3, J24.3, R21.1
/D11: A1.14 (D11), J2.14, J28.2
/D12: A1.15 (D12), D4.4 (DIN), J2.15
/D13: A1.16 (D13), J3.1
/HALL_OUT: J34.3, U9.2 (OUT)
/IP+: J31.2, U8.1 (IP+), U8.2 (IP+)
/IP-: J32.2, U8.3 (IP-), U8.4 (IP-)
/LX: C3.2, L1.1, R2.2, R4.1, U1.14 (LX), U1.15 (LX), U1.16 (LX), U1.23 (LX), U1.24 (LX), U1.25 (LX), U1.26 (LX), U1.28 (EPAD)
/OUT: J33.3, U8.7 (OUT)
/P5V: A1.30 (VIN), C4.1, D8.2 (A), J3.15, J14.1, J14.2, J14.3, J14.4, J14.5, J14.6, J19.2, J20.2, J21.2, J22.2, J23.2, J24.2, J25.2, J26.2, J27.2, L1.2, U5.3 (VI)
/RST: A1.3 (~RESET), A1.28 (~RESET), J2.3, J3.13, J37.2, J38.2
/RXD: A1.2 (D0/RX), J2.2
/SCL_3V3: J18.3, R22.2, U4.2 (SCLA)
/SDA_3V3: J18.4, R23.2, U4.3 (SDAA)
/TXD: A1.1 (D1/TX), J2.1
/VBUS_USBC: C13.1, D9.2 (A), D10.2 (A), J30.A4 (VBUS), J30.A9 (VBUS), J30.B4 (VBUS), J30.B9 (VBUS), R31.1, U6.2 (VIN), U6.16 (VBUS), U7.2
GND: A1.4 (GND), A1.29 (GND), C1.2, C2.2, C4.2, C7.2, C9.2, C10.2, C11.2, C12.2, C13.2, C14.1, C15.1, C16.2, D4.3 (VSS), D5.3 (VSS), D6.3 (VSS), J2.4, J3.14, J4.2, J5.1, J6.1, J7.1, J8.1, J9.1, J10.1, J11.1, J12.1, J13.1, J16.1, J16.2, J16.3, J16.4, J16.5, J16.6, J17.1, J17.2, J17.3, J17.4, J17.5, J17.6, J18.2, J19.1, J20.1, J21.1, J22.1, J23.1, J24.1, J25.1, J26.1, J27.1, J28.1, J29.2, J30.A1 (GND), J30.A12 (GND), J30.B1 (GND), J30.B12 (GND), J30.S1 (SHIELD), J33.1, J34.1, J35.1, J35.2, J35.3, J35.4, J35.5, J35.6, J35.7, J35.8, J35.9, J35.10, J35.11, J37.1, J38.1, JP2.1 (A), R6.2, R8.2, R11.2, R13.2, R26.2, R29.2, R30.2, R31.2, R33.2, RV1.3, RV2.2, U1.1 (PGND), U1.2 (PGND), U1.3 (PGND), U1.4 (GND), U1.8 (GND), U1.19 (GND), U1.20 (GND), U1.21 (GND), U1.27 (EPAD), U2.1 (S), U2.2 (S), U2.3 (S), U3.2 (V-), U4.4 (GND), U5.1 (GND), U6.5 (GND), U7.3 (GND), U8.5 (GND), U9.3 (GND)
unnamed: BZ2.1 (-), J1.1, U2.5 (D), U2.6 (D), U2.7 (D), U2.8 (D)
unnamed: BZ2.2 (+), D3.2 (A)
unnamed: C1.1, U1.9 (SS)
unnamed: C3.1, D1.1 (K), R1.2
unnamed: C5.1, R4.2
unnamed: C5.2, C6.1, R2.1, R3.2, R5.1, U1.5 (VFB)
unnamed: C8.1, R5.2
unnamed: C14.2, D10.1 (K), U7.5 (VCC)
unnamed: D2.1 (K), R6.1
unnamed: D4.2 (DOUT), D5.4 (DIN)
unnamed: D5.2 (DOUT), D6.4 (DIN)
unnamed: D7.1 (K), R13.1
unnamed: D7.2 (A), JP1.1 (A), R12.2, U3.4
unnamed: D8.1 (K), R26.1
unnamed: D9.1 (K), F1.1, J1.2, R9.2
unnamed: D11.1 (K), R9.1
unnamed: D3.1 (K), D11.2 (A)
unnamed: J27.3, R14.2
unnamed: J27.4, R15.2
unnamed: J27.5, R16.2
unnamed: J27.6, R17.2
unnamed: J27.7, R18.2
unnamed: J27.8, R19.2
unnamed: J27.9, R20.2
unnamed: J27.10, R21.2
unnamed: J28.3, U5.2 (VO)
unnamed: J29.3, SW3.2 (B)
unnamed: J29.4, SW4.2 (B)
unnamed: J29.7, SW5.1 (A)
unnamed: J31.1, J32.1
unnamed: J31.3, J32.3
unnamed: JP2.2 (B), U4.5 (EN)
unnamed: JP3.1 (A), R27.1
unnamed: JP4.1 (A), R28.1
unnamed: R1.1, U1.18 (BST)
unnamed: R3.1, RV2.1
unnamed: R10.2, R11.1, SW2.2 (B), U3.1 (+)
unnamed: R33.1, SW1.1 (A), U2.4 (G)
unnamed: RV1.2, U3.3 (-)
VBUS: C9.1, D2.2 (A), F1.2, J5.2, J6.2, J7.2, J8.2, J9.2, J10.2, J11.2, J12.2, J13.2, R7.1, R32.1, U1.10 (VIN), U1.11 (VIN), U1.12 (VIN), U1.13 (VIN), U1.29 (EPAD)

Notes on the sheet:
Actuator Outputs
LEDs
Current Sensors
VBAT to P"5V" Buck Conversion
Jumpers on PCB Default (MPU6050): 5V GND SCL SDA NC NC NC INT Can change to (LSM6DS33): 5V GND SDA SCL NC NC INT INT
Power In, Reverse Polarity and Overcurrent Protection
MicroController
Breadboard Power Headers
USB-C PD Negotiaton and Safety E-Switch
RC IN
Photoresistor Input
I2C Connections
12K - 5V 136K - 7.5V

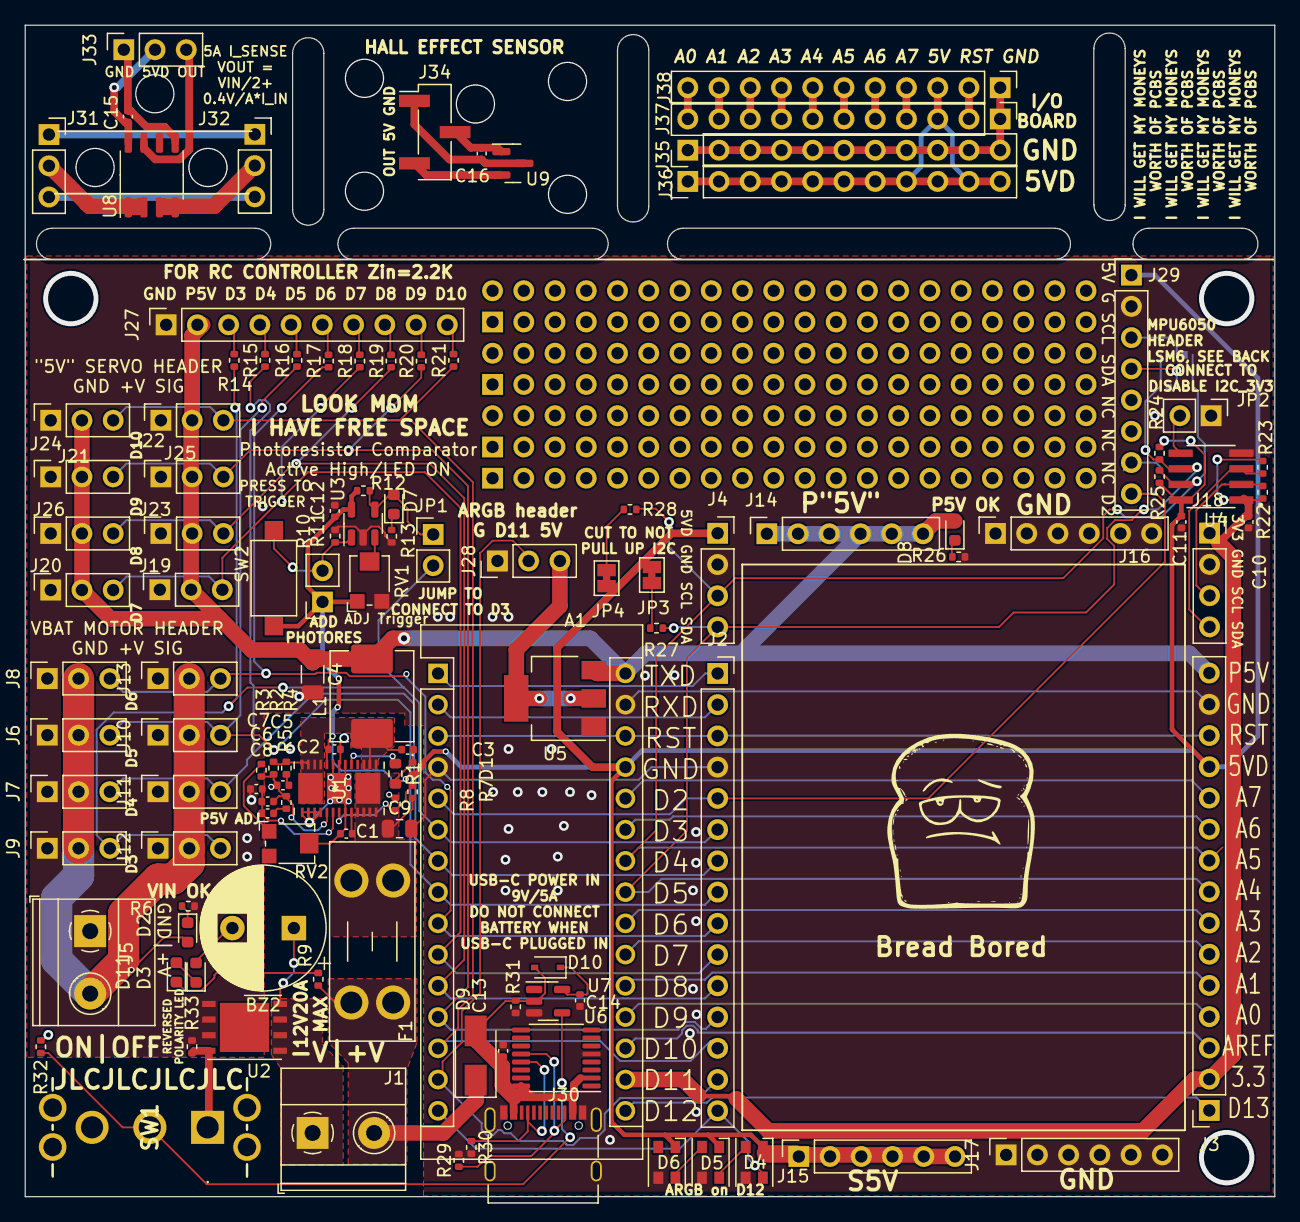
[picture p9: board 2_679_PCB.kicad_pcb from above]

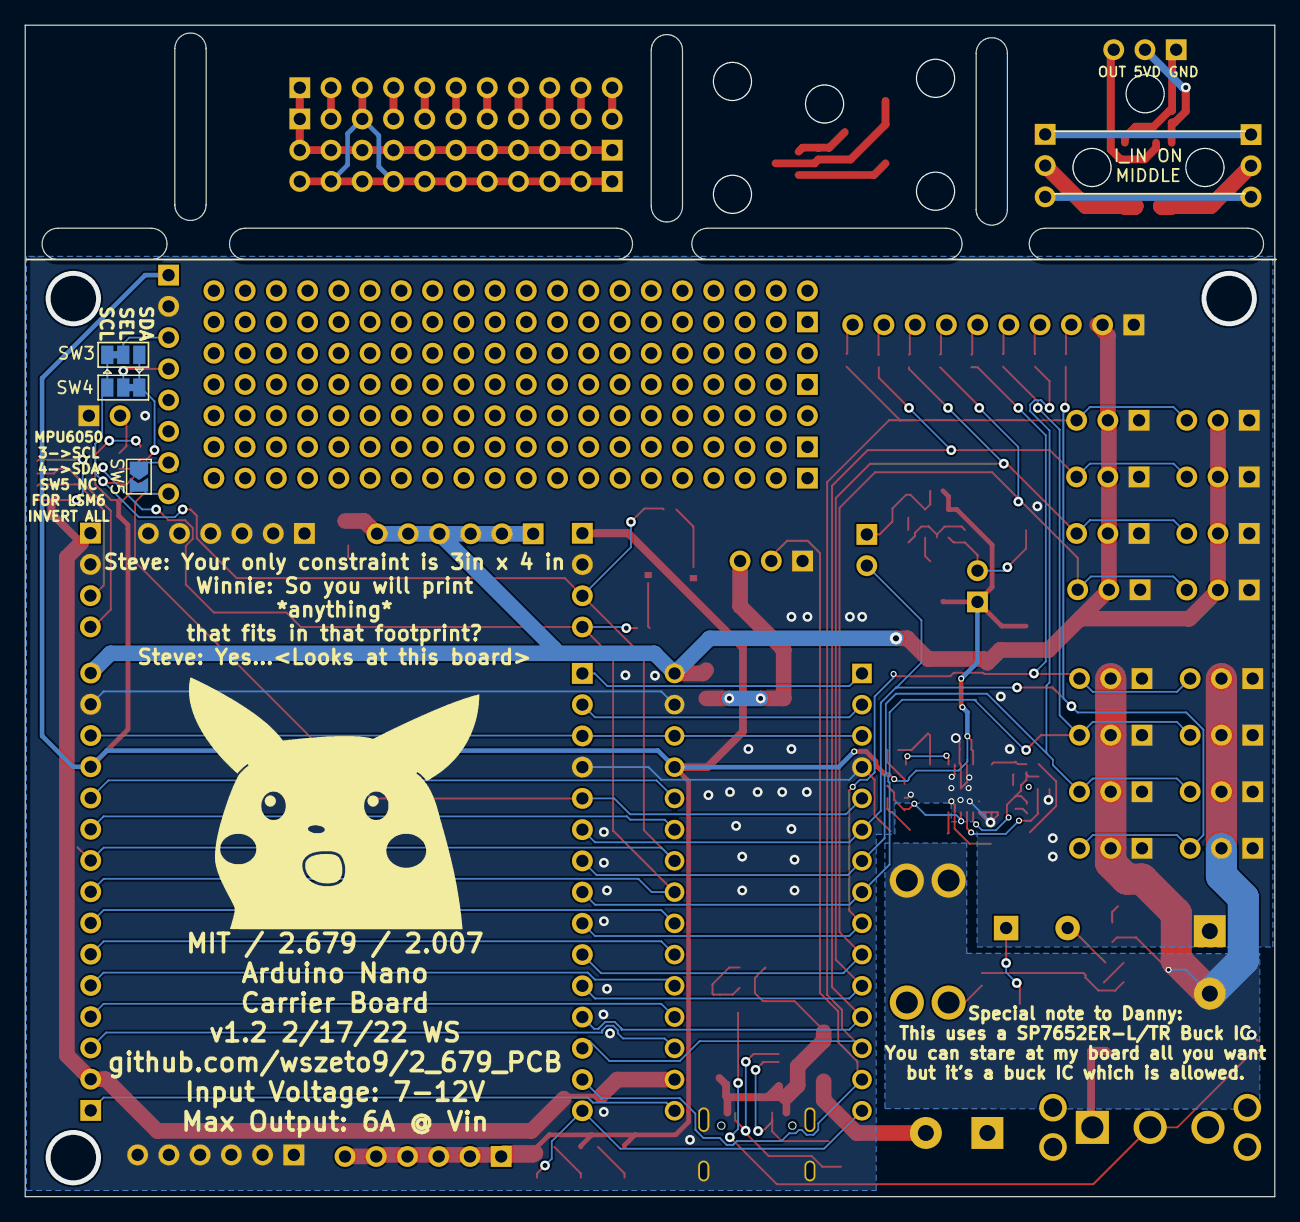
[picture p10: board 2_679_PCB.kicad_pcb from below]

Board: 2 copper layers, 101.6 x 95.2 mm, 122 parts (3 on the bottom side), 81 nets.

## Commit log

2022-03-16 fully defined states for inverter
    [2_679_PCB-B_Cu.gbr, 2_679_PCB-B_Mask.gbr, 2_679_PCB-B_Paste.gbr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]
2022-03-16 changed e-pads
    changed e-pads
    [2_679_PCB.kicad_pcb, 2_679_PCB.kicad_sch]
2022-03-16 Doubled reverse bias LEDs
    Prevents LEDs from blowing up from 5V max reverse bias
    [2_679_PCB-B_Cu.gbr, 2_679_PCB-B_Mask.gbr, 2_679_PCB-B_Paste.gbr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]
2022-03-16 fixed DRC
    trace was routed incorrectly
    [2_679_PCB-B_Cu.gbr, 2_679_PCB-B_Mask.gbr, 2_679_PCB-B_Paste.gbr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]
2022-03-17 added breakout boards
    Added boards to increase space use of the board to 4x4"
    [2_679_PCB-B_Cu.gbr, 2_679_PCB-B_Mask.gbr, 2_679_PCB-B_Paste.gbr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]
2022-03-19 updated BOM
    [2_679_PCB.kicad_sch, 2_679_PCB_digikey_BOM.csv]
2022-03-20 added usb-c digikey part number
    [2_679_PCB.kicad_sch]
2022-04-02 added arduino board and power distribution
    [2_679_PCB.kicad_pcb, arduino_usb_c.kicad_pcb, arduino_usb_c.kicad_sch]
2022-04-04 added power management board
    [arduino_usb_c-B_Cu.gbr, arduino_usb_c-B_Mask.gbr, arduino_usb_c-B_Paste.gbr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]
2022-07-10 added step files
    [2_679_PCB.kicad_pcb, arduino_usb_c.csv, arduino_usb_c.kicad_sch]

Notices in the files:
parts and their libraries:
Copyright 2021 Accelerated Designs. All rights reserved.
